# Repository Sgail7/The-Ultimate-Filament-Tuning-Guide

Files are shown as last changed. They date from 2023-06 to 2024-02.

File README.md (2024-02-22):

# The Ultimate Filament Tuning Guide

### How to tune 3D printer filaments to perfection!

This guide details how I tune in my 3d printing filaments. It takes approximately 80 grams of filament and a few hours of time, including print times. If your printer profiles are tuned in properly, following this guide will give you the best settings possible for your various filaments. This is **NOT** a guide on how to fine tune your printer's motion system and settings, for that, please see [Ellis' Excellent Print Tuning Guide](https://ellis3dp.com/Print-Tuning-Guide/). Both Ellis' and myself's Flowrate Test work, although I believe that my method gives more accurate results. Whichever you would like to use is up to you.

### Things to Know

This guide assumes that you are using [Klipper firmware](https://www.klipper3d.org/), but everything except for the probe calibration method is transferrable to any other 3D printer firmware. It also assumes that your are using [PrusaSlicer](https://www.prusa3d.com/page/prusaslicer_424/), however most, if not all, of these settings can be found in other slicers, although they may have slightly different names. Lastly, it assumes that you know how to slice for your machine and have a general knowledge of what the settings in your slicer modify. There is a plethora of knowledge online if you are confused. I highly recommend just looking up whatever you would like to know that isn't explained here.

All needed models and .3mf files are included in the [Tuning Models](Tuning-Models) folder. The guide will detail which file to use for each test. I highly recommend following the [Per Filament Steps](#per-filament-steps) section of the guide in order, as it will give the least variation in results, but you may follow this guide in whatever order you choose.

If you notice slight problems that can be attributed to a wrong interpretation of a test's results, I recommend finishing the entirety of the [Per Filament Steps](#per-filament-steps) section, and then going back and fixing the issue. Doing this prevents any untuned variables from skewing your retests, and means that once you fix the problem, everything is done and you can move on to printing!

# How to import 3MF files

Import the file into PrusaSlicer by **dragging and dropping it into the program**. If you use the `"Import Project..."` or `"Add..."` buttons, it will import the file with my personal profiles, which is a major headache. When the window shown below appears, make sure to select `"Import 3D models only"`. This will prevent you from importing my personal profiles and, again, will save a lot of headache getting rid of those.

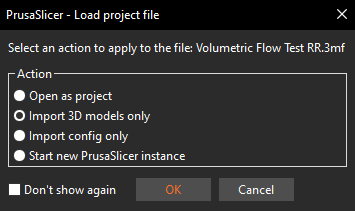
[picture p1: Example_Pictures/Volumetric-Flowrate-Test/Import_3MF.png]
3MF


# Feedback and Additions

This guide was created through my years of experience and the accumulated knowledge of this community. That being said information can be wrong, so if there is an issue with this guide, please open an issue on this repo! I'll get back to you and fix it as soon as I can. It doesn't matter if its a typo or an entirely wrong section, if something's not right, I'd like to make sure it's made right. 

If there is something that you think should be added to this guide, please submit a pull request or an issue! For example, I've been looking for good ways to tune the `Dynamic Fan Speeds` and `Enable Fan if Layer Print Time is Below:` settings!

Lastly, if you use this guide and find it helpful, please give it a star! It helps me know that other's find this guide useful and would benefit from it being updated whenever I figure out something new.

# THE GUIDE

- [One-Time Steps](#one-time-steps)
    - [First Layer Calibration](#first-layer-calibration)
    - [Elephant's Foot Compensation](#elephants-foot-compensation)
    - [Infill/Perimeter Encroachment Test](#infillperimeter-encroachment-test)
    - [Bridge Flow Rate Calibration Test](#bridge-flow-rate-calibration-test)

- [Per Filament Steps](#per-filament-steps)
    - [Temperature Test](#temperature-test)
    - [Volumetric Flowrate Test](#volumetric-flowrate-test)
    - [Linear Advance Test](#linear-advance-test)
    - [Flowrate Test](#flowrate-test)
    - [Retraction Test](#retraction-test)
    - [Fan Speed Test](#fan-speed-test)
    - [Minimum Layer Time Test](#minimum-layer-time-test)
    - [Minimum Layer Speed Test](#minimum-layer-speed-test)
    - [Validate Tuning Results](#validate-results)

- [Optional Steps](#optional-but-still-recommended-steps)
    - [Material Expansion/Contraction Calibration](#material-expansioncontraction-calibration)
    - [Retract/Unretract Speeds](#retraction-and-unretraction-speed-tuning)
    - [TMC Register Tuning](#tmc-register-tuning)
    - [VFA Testing and Tuning](#vfa-tuning-tests)

- [Troubleshooting Results](#troubleshooting-results)
    - [Validation Model Issues](#validation-model-issues)

# One-Time Steps

## **First Layer Calibration**

If using an automatic bed probe, first follow the klipper docs for [Probe Calibration](https://www.klipper3d.org/Probe_Calibrate.html).

- **Note:** The following is less of a one-time step and more of a "you should do this biweekly" step.

If your printer has bed leveling springs, run the `BED_SCREWS_ADJUST` command and use either a 0.10 mm feeler gauge or a sheet of A4 paper to adjust the bed to be in parallel with the gantry. Do this even if you have an automatic leveling probe installed.

When the above have been completed, make a cube in your slicer. Scale it to approximately half of the total size of your bed, then unlock the scaling and change the z height to be equal to the height of your first layer. Run the print while sitting infront of your printer. As the print progresses, use the babystepping feature found in your web interface to iteratively raise or lower the bed until your layer lines look perfect. Once you reach a point you are happy with, you can either let the print complete or cancel the print. Pull the layer of filament off of the bed and inspect the underside to make sure that your final adjustment is correct. Run `Z_OFFSET_APPLY_PROBE` then `SAVE_CONFIG` to save your new z-offset.

## **Elephant's Foot Compensation**
This isn't so much of a step as it is something that I just recommend doing. Elephant's foot compansation shrinks the first layer by the amount specified in the x and y axes so that your first layer squish doesn't artifically create a bigger-than-wanted footprint on the bed. I set this value at 0.1 mm to start. Typically it sits somewhere between 0 mm and 0.2 mm. I wouldn't recommend going above 0.2 mm unless you have a leveling problem, in which case you should redo the above step. If you make the elephant's foot compansation value too big, you may cause the first layer to be too small, preventing good layer stacking on top of it. You can read more about this feature [here](https://help.prusa3d.com/article/elephant-foot-compensation_114487).

## **Infill/Perimeter Encroachment Test**
- Uses [Perimeter-Overlap-Test](Tuning-Models/Perimeter-Overlap-Test.3mf)

Import [Perimeter-Overlap-Test](Tuning-Models/Perimeter-Overlap-Test.3mf) into your slicer. Make sure that there is at least two layers of infill between the top and bottom solid layers. Print out the file and check for gaps and pin holes at the edge of the top layer. The best value for your Infill/Perimeter overlap is where these gaps and holes disappear, but there is not over extrusion in the corners of the cube. The screenshot below shows what Perimeter Overlap Percentages each test model is printed at.

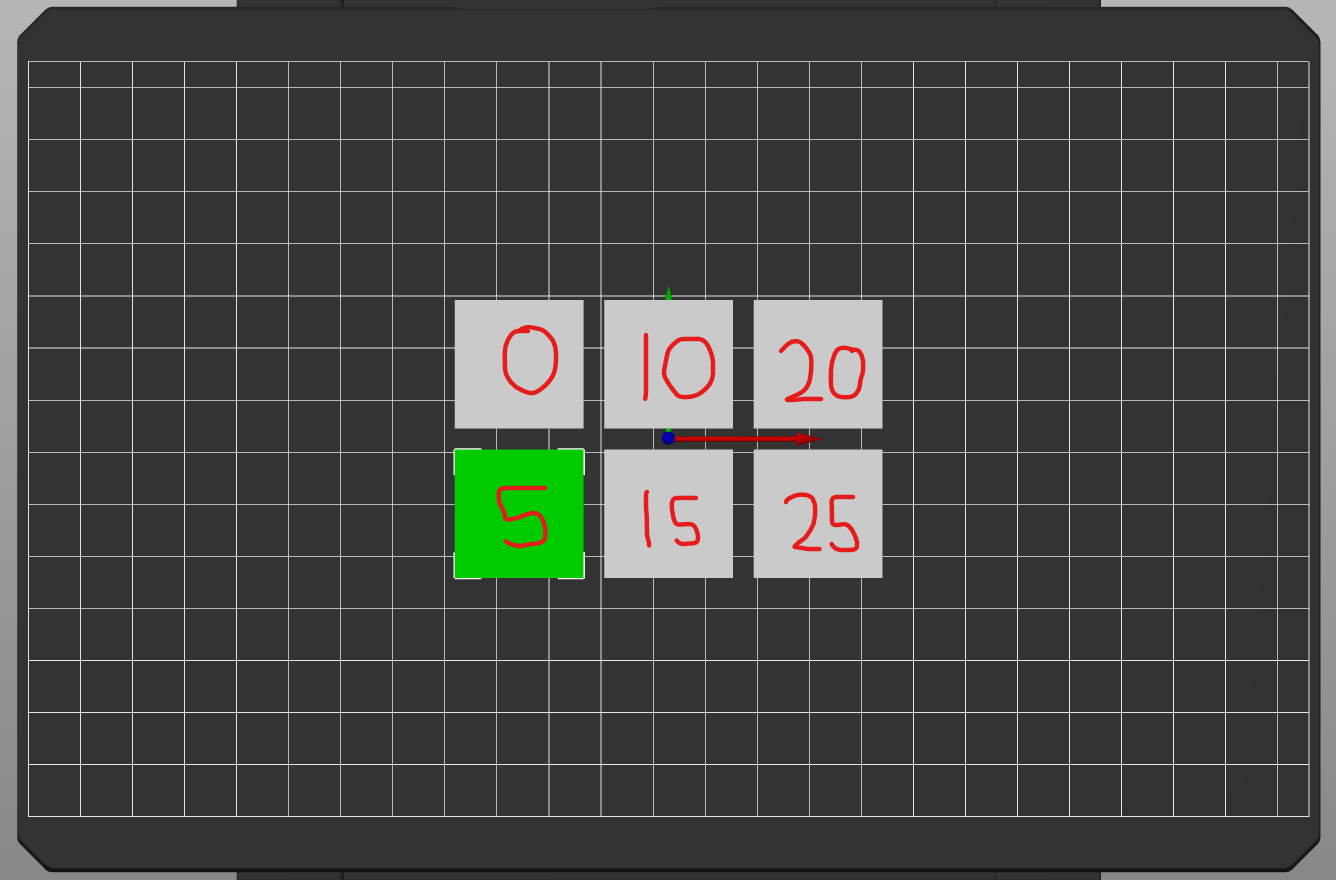
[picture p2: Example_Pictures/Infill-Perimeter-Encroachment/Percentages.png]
Perimeter-Overlap-Percentages


<details><summary>Click here to See Example</summary>
<p>

Overlap-Example

Here is an example of perimeter encroachment that I printed on my heavily modified Ender 3. The values used are the same as the screenshot from the slicer.

- A symptom of too little perimeter encroachment can be found in the 0% and 5% squares.
    - The pin holes at the edges of the top layer indicate that not enough filament is being extruded to properly bond to the walls.

- The 10% through 25% squares all show signs of too much perimeter encroachment.
    - The point where the top layer meets the walls causes a buldge at that contact point, rasing the edge of the top surface.
    - The beginning corner of the higher percentage squares can be seen to be severely over extruded. The 10% square has this also, but that is because the print ended in that spot.
    - It may be hard to see on camera, but the 20% and 25% squares also have ridges on their top surfaces that correspond to the extrusion lines on that surface, which is a result of over extrusion

From this test I can deduce that my ideal perimeter encroachment lies somewhere between 5% and 10%. To find this ideal encroachment, you can either change the values of the squares and run the test again (i.e. 5%, 6%, 7%, etc...), or you can change it as you do prints and finalize it when the top surface of those prints looks ideal.

Personally, I would recommend changing it by small amounts as you do prints. It won't affect your prints much, and will save you time and filament on another test print.

</p>
</details>

**Note**: Bigger nozzles usually have more difficulty closing these gaps. I recommend checking [this section of Ellis' print tuning guide](https://ellis3dp.com/Print-Tuning-Guide/articles/infill_perimeter_overlap.html) for more solutions.

## **Bridge Flow Rate Calibration Test**
- Uses [Bridge-Flow-Tuning](Tuning-Models/Bridge-Flow-Tuning.3mf)

This calibration should only be done after you have calibrated your fan speed and have figured out what a good bridging speed for your printer is. Make sure that your bridging still suffers even on 100% fan speed before using this feature. If you are satisfied with the bridging performance and dimensional accuracy of holes, skip this step, otherwise do the following.

Import [Bridge-Flow-Tuning](Tuning-Models/Bridge-Flow-Tuning.3mf) into your slicer. This file will print a group of the test model with bridge flow rates ranging from a bridge flow ratio of 1.0 to 0.4. The screenshot below shows the ratios that each test model is printed at.

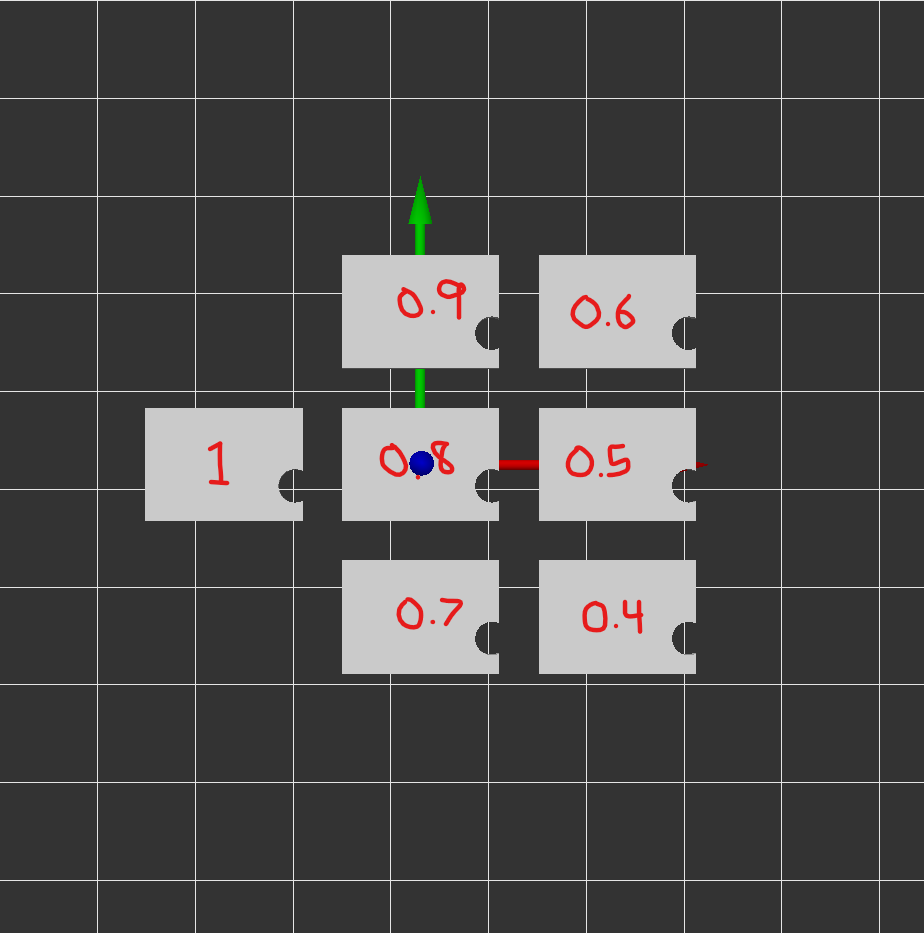
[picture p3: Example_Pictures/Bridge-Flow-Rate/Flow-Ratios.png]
Bridge-Flow-Ratios


Once these are printed, you are looking for the highest flow ratio that does not produce drooping at the top of the holes. You want to adjust this ratio as little as possible, the closer you can stay to a ratio of 1.0, the better. Once you have found your ideal bridge flow ratio, you can input the setting in the location shown in the screenshot below.

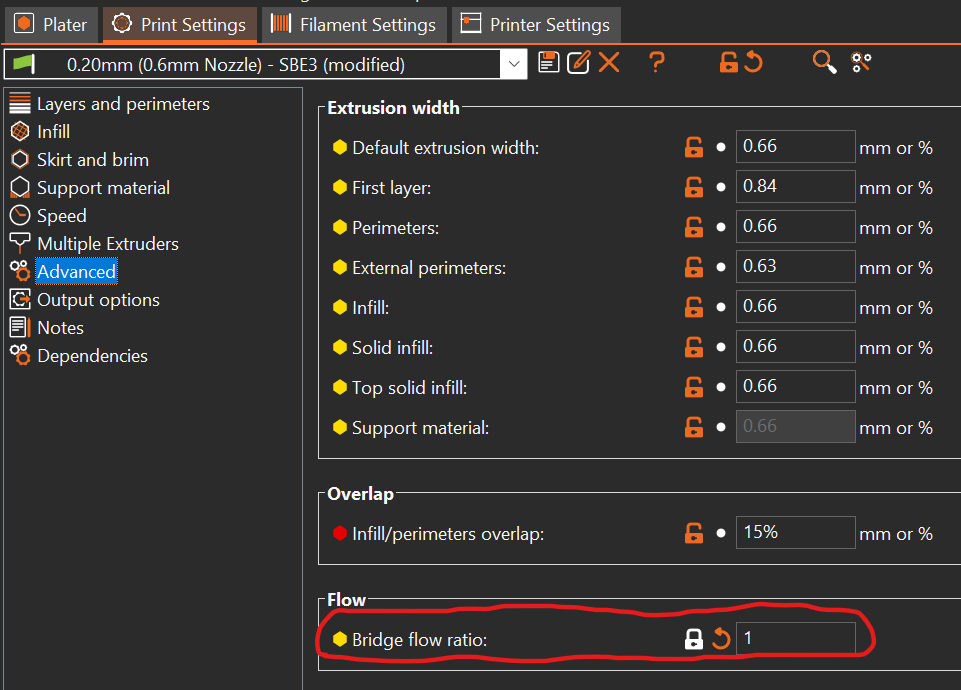
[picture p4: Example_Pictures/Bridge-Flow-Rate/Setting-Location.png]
Location-Bratio


Your final result should look something like this:

<details><summary>Click here to See Pictures</summary>
<p>

Here are a few pieces of the bridge flowrate test that I printed on my heavily modified Ender 3.

- This example was printed with a 1.0 ratio.
    - The top of the hole shows plastic that is severely protruding into the hole. This indicates that the flowrate is too high and needs to be lowered.

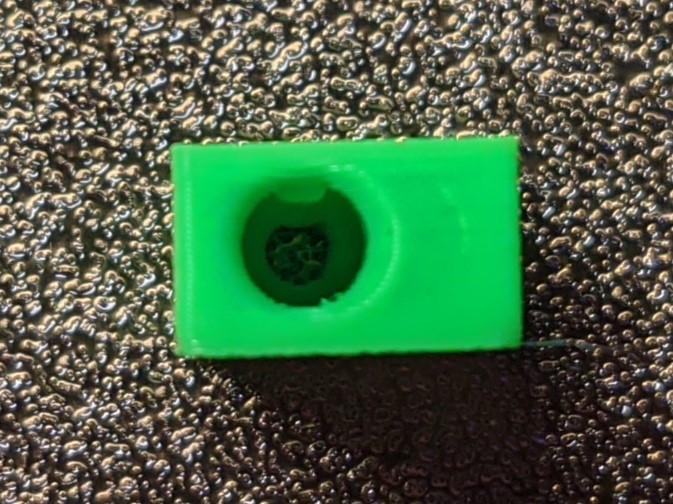
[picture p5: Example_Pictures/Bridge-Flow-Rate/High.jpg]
High


- This example was printed with a 0.4 ratio.
    - At the top of the hole, the bridging lines seem to be barely touching each other and in some cases being stretched thin near their ends. This indicates that the flowrate is too low and needs to be raised.

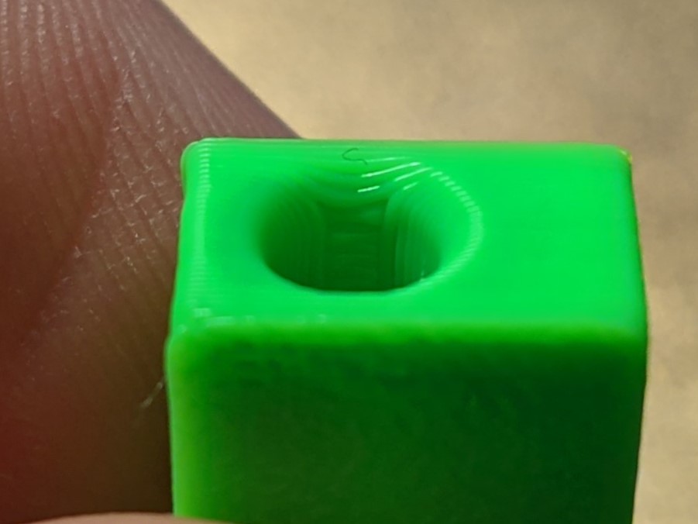
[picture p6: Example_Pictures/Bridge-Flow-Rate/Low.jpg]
Low


- This example was printed with a 0.7 ratio.
    - The bridge lines at the top of the hole are nice and even, touching their neighbors without protruding into the hole. This is the correct flowrate for this printer and infact is the flowrate I use for a 0.20 mm layer height, which is what is pictured.

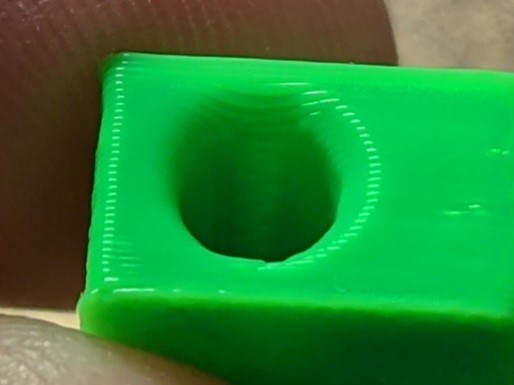
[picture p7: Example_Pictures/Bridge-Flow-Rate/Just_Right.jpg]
Correct


- **Note:** It is very hard to take pictures of this feature because of the size of the pieces and lighting. I promise that the differences between the flowrate ratios are much more clear when doing this test in real life.

</p>
</details>

**Note**: You will have to test this for every layer height profile that you have for your printer. Since different volumetric amounts are output at different layer heights, the amount of bridge flow rate reduction needed will vary. Generally, more is needed for larger layer heights, and less is needed for smaller layer heights. You are trying to get away with as little flow reduction as possible. Going too low on the multiplier may cause poor support for the layers on top of it or, in extreme cases, a breaking of the filament flow, causing the bridge to fail entriely (you will have to make a conceited effort to achieve the latter).

# Per Filament Steps

## **Temperature Test**

**Note:** For this test, you will need to unlatch your extruder in some way. Whether that be removing the tension knob on a bondtech gear set or holding the lever arm open on a Mk8 style extruder. Essentially you don't want the extruder gear(s) touching the filament in anyway, if possible.

Read the manufacture's rated temperatures for your filament. Choose a starting point that is 10°C below the lowest temperature, and an ending point that is 10°C higher than the highest temperature. For example, a range of `190°C - 220°C` would mean that you want to run the hotend through a temperature range of `180°C - 230°C`. Set your hotend to your starting point and let it stabilize.

Unlatch your extruder and grip the filament with your hand. The goal is to push filament through the extruder with as constant of a pressure as possible. Once in position, set the temperature of your hotend to your ending point, and start pushing. Keep a close eye on the temperature as it rises and as you keep pushing.

You will notice that the filament starts moving noticably faster when the hotend hits certain temperatures. Make a note of those points in your head as you push the filament. Once the hotend reaches your chosen ending point, you can stop pushing the filament. Turn your hotend heater off and relatch your extruder.

Write down the tempatures where you noticed the resistance on the filament decrease. Generally, picking a temperature in the middle of the manufacture's rated temperatures is a good all around setting. Avoid the trap of setting the filament temperature as low as possible, as it can lead to extruder skipping and extruded lines that were not fully melted in the hotend.

Continuing the example from earlier, say there's a filament with a rated temperature range of `190°C - 220°C`. I'll set my hotend to run through a range of `180°C - 230°C` for this test. I do the test as described above, and I find that the points at which the resistance on the filament dropped were `190°C, 210°C, and 230°C`. Wanting a good overall setting, I'll choose `210°C` as the temperature for this filament.

### Good Rules of Thumb

- Generally, the best temperature is somewhere in the middle of the recommended temperatures on a standard 0.4mm brass nozzle, however, this is not a steadfast rule. Hardened steel nozzles tend to need to run about 10-15 C hotter than brass to compensate for their lower heat transfer coefficient.

- Adding 5°C to your chosen temperature can be beneficial if you tend to prefer setting your filaments to lower temperatures. It will prevent your filament from being too resistive to extrusion while still maintaining the qualities that you are looking for.

- If pushing for high volumetric flow rates, chosing the highest temperature where the resistance on the filament dropped is the best option for this test. Keep in mind that doing this will cause lower volumetric flow rate areas in your models to string more heavily.

## **Volumetric Flowrate Test**

- Uses [Volumetric-Flow-Test-RR.3mf](Tuning-Models/Volumetric_Flow_Test.3mf)
- This test was designed by Yathani on Printables! Go check it out here: [Volumetric Flow Test for RatRig V-CORE3](https://www.printables.com/model/328223-volumetric-flow-test-for-ratrig-v-core3)

This test works by increasing your printer's feedrate by 100% every 5 mm in z-height. For a standard flow hotend, you'll want to step up in 2 mm<sup>3</sup>/s increments; for high-flow hotends, you'll want to step up 2-5 mm<sup>3</sup>/s increments, depending on the advertised maximum flowrate of your hotend. The final volumetric flowrate will be 12 times the starting flowrate.

Volumetric flow rate can be calculated as:

$$VFR=Layer height * Layer width * Layer Speed$$

Because layer height and layer width stay constant during a print, we want to change the layer speed of the external perimeters to control the volumtric flowrate of the test. Rearranging the equation, and using 2 mm<sup>3</sup>/s as the target volumtric flow rate, we can find our needed external perimeter speed for this print.

$$Layer Speed=2/(Layer width*Layer height)$$

Using a 0.4mm layer width with a 0.2mm layer height as an example, we obtain this answer

$$Layer Speed=2/(0.4*0.2)$$

$$Layer Speed=25mm/s$$

Turn on Spiral Vase mode, set your external perimeter speed to the value you obtain, and run the print. If you feel that the final volumetric flow rate is far past the limit of your hotend, you can scale the model in z-height only in PrusaSlicer to obtain a lower final volumetric flow rate.

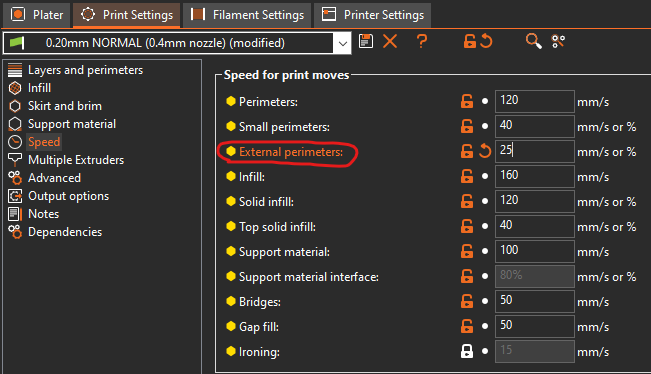
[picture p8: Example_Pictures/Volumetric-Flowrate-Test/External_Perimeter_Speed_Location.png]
External-Perimeter-Location


Once this test is completed and your printer is cooled, I highely recommend either restarting the printer, or, if using Klipper, issuing a `FIRMWARE_RESTART` command.

## **Linear Advance Test**
- Follow [Ellis' Print Tuning Guide](https://ellis3dp.com/Print-Tuning-Guide/) for this and use [his online calibration tool to generate your gcode.](https://ellis3dp.com/Pressure_Linear_Advance_Tool/) Do interations down to 0.001 for Direct Drive extruders, and down to 0.01 for Bowden extruders.
- [Ellis' Pressure Advance Documentation](https://ellis3dp.com/Print-Tuning-Guide/articles/pressure_linear_advance/pattern_method.html)
- [Klipper Pressure Advance Documentation for Extra Information](https://www.klipper3d.org/Pressure_Advance.html)

- **Note:** If flowrate is wildly off target, running pressure advance and using the value found can exacerbate the issue. In these instances, running the Linear Advance Test again after the Flowrate Test can alleviate these issues. Typically, anything greater than a 10% deviation of flowrate requires a recalibration of Linear Advance with the newly found flowrate.

As I've explained in the [Retraction/Unretraction Speed Tuning Section](#retraction-and-unretraction-speed-tuning), I am not a fan of external gcode generators. However I feel the need to explain my preference for this method of pressure advance calibration, as I used to recommend the [Official Klipper](https://www.klipper3d.org/Pressure_Advance.html#tuning-pressure-advance) method.

I have found that using the Klipper Tuning Tower Method has reliably and repeatedly given me pressure advance values that are higher than what a filament requires. These values lead to print artifacts that round off corner entries, create wall separation, and cause very high [Infill/Perimeter Overlap](#infillperimeter-encroachment-test) values to be needed. Because each of these issues can also be caused by other variables, and they are seemingly unrelated when not considering specifically pressure advance, it can lead one on a wild goose chase trying to solve the issue.

In addition to that, it can be very hard to tell what a good pressure advance value is due to each of the corners of the model showing different amounts of artifacting. Trying to measure the inside small corners of the model is more accurate, but is a pain with calipers and impossible with a micrometer of reasonable size.

In contrast, Ellis' pattern method is more accurate, faster, and uses less filament. It's only two downsides are that it requires iterations and an external gcode generator. Despite that I exclusively use this method now to avoid the afformentioned issues and gain from the afformentioned benefits.

## **Flowrate Test**

Create a 25mmx25mmx25mm cube in your slicer. Set your slicer to Spiral Vase mode, and take note of your external perimeter line width. You should be printing an object similar to the following.
    
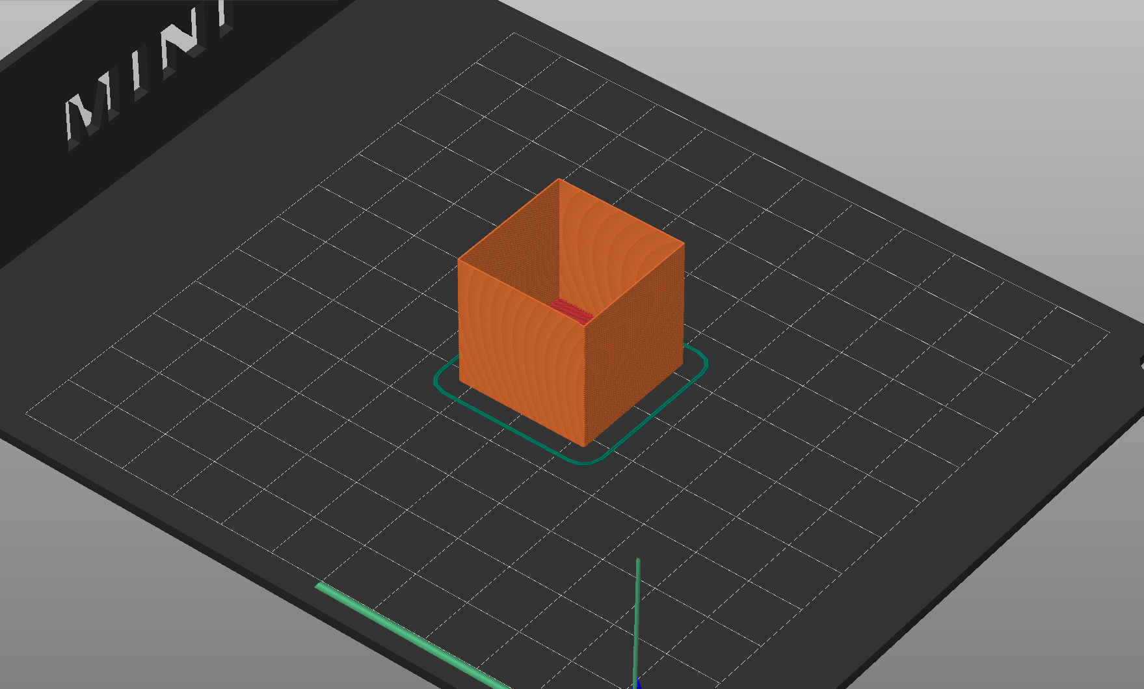
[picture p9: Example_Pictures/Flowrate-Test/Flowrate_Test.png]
Flowtest-Example


Allow the cube to cool before removing it from the buildplate, then take a pair of calipers and measure the thickness of each wall. I only recommend putting the calipers, at maximum, ~2mm down the sides of the cube to prevent excessive variation from layer wobble. Take the average of your measurements, then divide your line width by that average. This will give the correct flowrate for the tested filament.

Example: Line width is set to 0.45mm. The cube's walls are found to have a line widths of 0.45, 0.47, 0.48, and 0.46, respectively. The average of those line widths is equal to:

$$Average=(0.45+0.47+0.48+0.46)/4$$

$$Average=0.465mm$$

To find the needed flowrate multiplier, divide the original line width by the found average:

$$Flowrate=0.45/0.465$$

$$Flowrate=~0.968$$

This would be the new flowrate multiplier for your filament. If you notice underextrusion issues in your prints, try increasing your multiplier by 0.01.

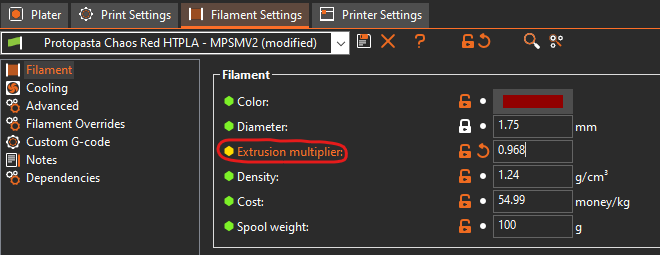
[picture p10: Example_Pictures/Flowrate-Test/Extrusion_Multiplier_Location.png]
Flowrate-Location


- +-2% flow rate is negligible due to variation of filament diameter. In other words, if your result returns a number between 0.98 and 1.02, don't change your flow rate, it will cause more problems than it will solve.

## **Retraction Test**

- If you haven't noticed any problems with stringing, and don't notice any in the Fan Speed Test, this step can be skipped. Generally, with a good direct drive setup, the only filaments that will need a different retraction value are very soft flexible filaments and exotic filaments such as Carbon Fiber filled PLA.

Take the config that you have been using so far, and export it from PrusaSlicer. 
    
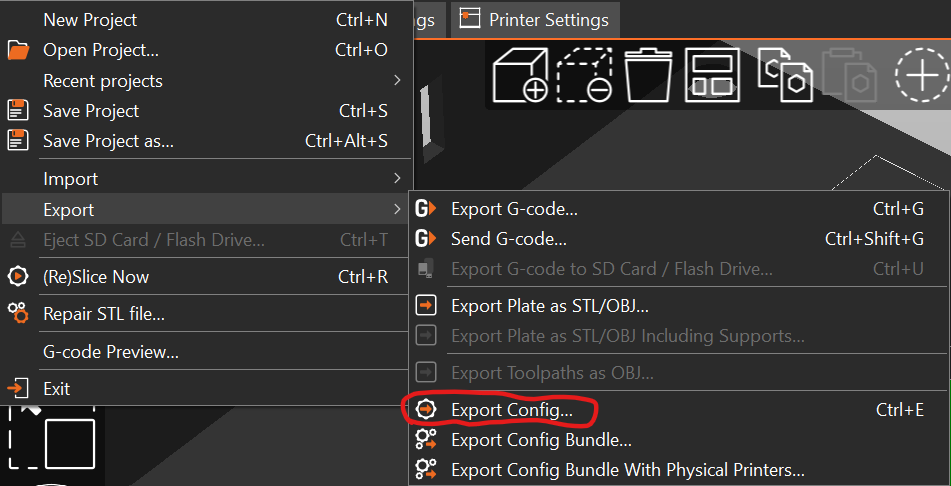
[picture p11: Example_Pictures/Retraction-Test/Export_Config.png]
Config-Export

    
Import it into SuperSlicer and save it. Now, use the built in Retraction Calibration that SuperSlicer has to determine the retraction needed for your particular filament. Read through the prompt that appears when you set up the test, it will tell you everything that you need to know to preform it.

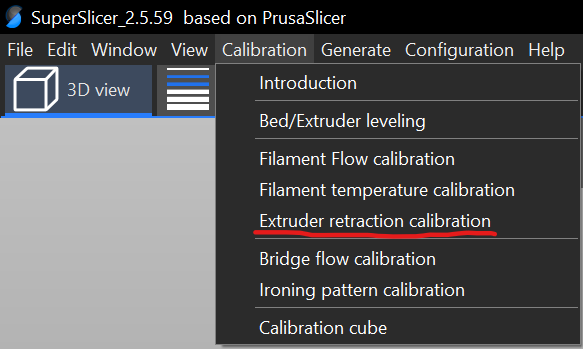
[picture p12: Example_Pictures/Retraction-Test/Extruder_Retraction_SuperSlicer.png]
SuperSlicer-Retraction-Test


## **Fan Speed Test**

- This test was designed by Abyss on Printables! Go check it out here: [Ultimate Fan Speed Test V3](https://www.printables.com/model/200347-ultimate-fan-speed-test-v3)

**Note:** Fan speed is generally forgiving. If you are getting worse results than expected you can raise or lower any of the fan speeds you set in this step. This step always gets me perfect fan speeds, but it may take some practice before you gain a feel for how to choose settings with this method. Essentially, you're not locked in to what you choose, just use it as a guideline.

- Import [Ultimate_Fan_Test_v3_ABYSS.stl](Tuning-Models/Ultimate_Fan_Test_v3_ABYSS.stl) into your slicer. Use a 0.2mm layer height and change your cooling settings to the following.

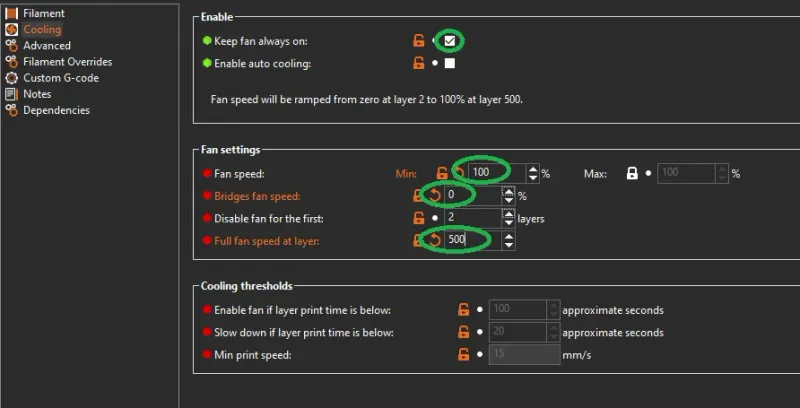
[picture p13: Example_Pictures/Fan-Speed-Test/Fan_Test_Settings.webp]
Fan_Speed_Settings


This will cause your fan to spin progressively faster as the model is printed, starting at 0% fan speed and ending at 100% fan speed. When the model is finished, take a look at each marked bar and the area above it. Choose the lowest fan speed that gives good results as your minimum fan speed. Generally, no curling and decent to good looking bridges are what to look at for this setting. Look at the bridging sections and choose the one that looks the best to you, that is your bridging fan speed.

You may want to take a picture of your model, because the next step involved intentionally breaking it apart. Start from the top of the model and work your way down, breaking it apart section by section. The sections will get harder to break apart as the fan speed at the point in the model gets lower. As you break it apart, feel for where the model gets harder to snap. There should be a point where it doesn't get any harder, and that is where your maximum layer adhesion is achieved. Take note of the highest fan speed at which the model has the same resistance to breaking as your chosen minimum fan speed. Set this fan speed to your maximum fan speed.

## **Minimum Layer Time Test**

- Uses [Minimum-Layer-Time-Test.3mf](Tuning-Models/Minimum-Layer-Time-Test.3mf)

Set your minimum layer time to 5 seconds and print this model. If the outer walls of the print curl up, increase the minimum layer time by two seconds. Print the model again with the new minimum layer time setting and check if there is any curling. Repeat this process until the walls print flat. Whatever you minimum layer time is at that point is the ideal value for that setting.

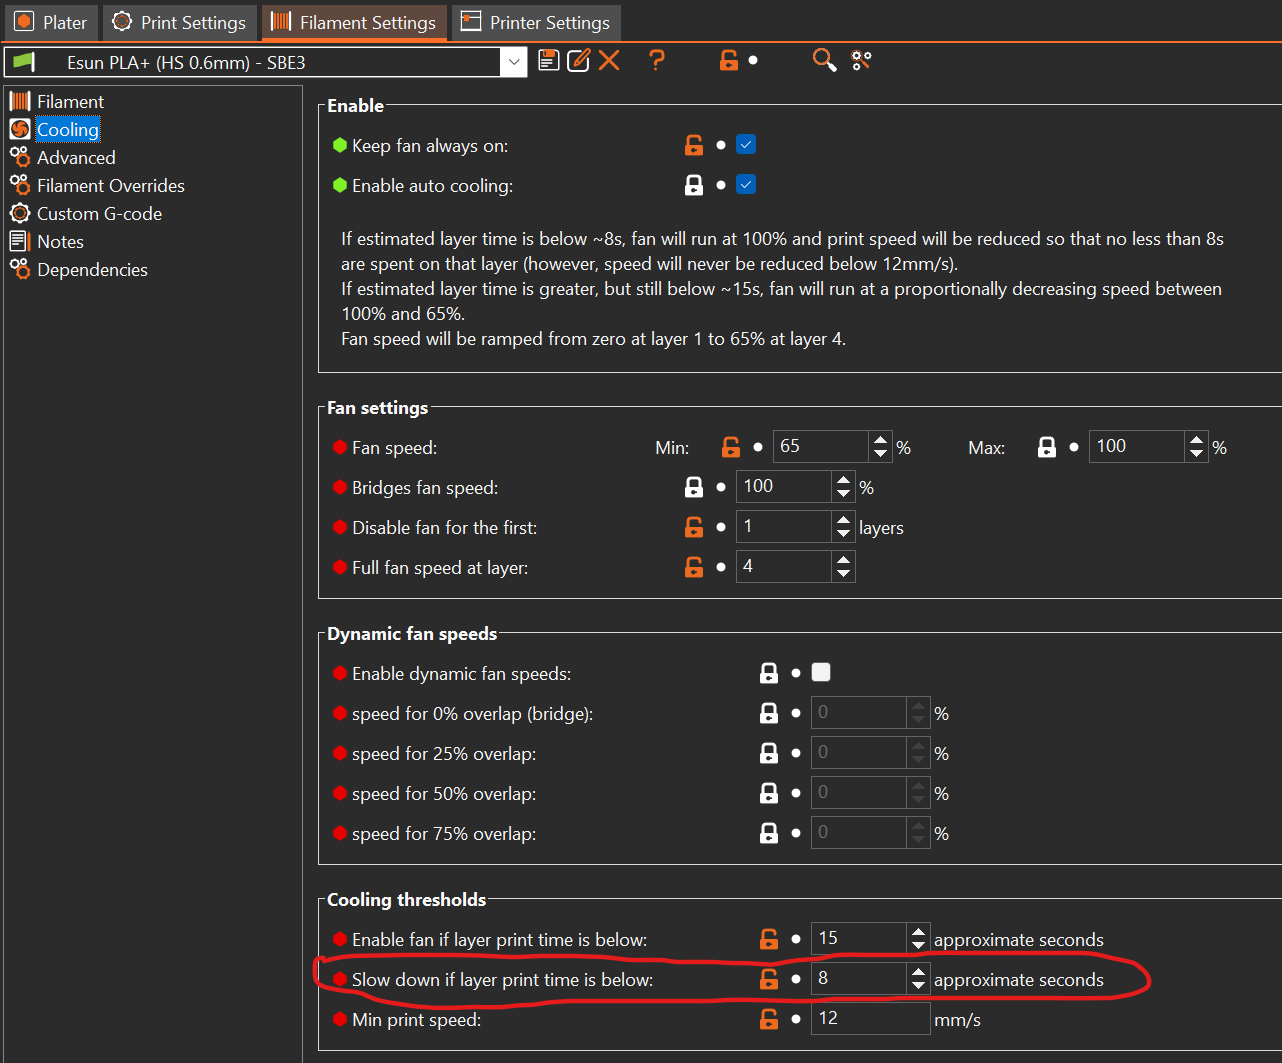
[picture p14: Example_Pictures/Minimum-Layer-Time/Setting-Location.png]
Location-Ltime


**Note:** For some filaments, there may not be a minimum layer time value that will completely eliminate curling. If this is the case, you can try lowering your printing temperature by a few degrees or upgrading your cooling setup. Otherwise, just choose the setting that gives the best results, even if they aren't perfect.

## **Minimum Layer Speed Test**
- Uses [Minimum-Layer-Speed-Cone.stl](Tuning-Models/Minimum-Layer-Speed-Cone.stl)

I recommend printing 5 copies of this model set at the following minimum layer speeds, `15 mm/s, 12 mm/s, 10 mm/s, 8 mm/s, 5 mm/s, and 3 mm/s`. Label each of the models as you print with a sharpie or other method, so that you do not forget which one is which. Put the printed models side by side and compare them to see which has the least amount of deformed plastic at the top of the model. Set this speed as your minimum layer speed.

**Note:** The upper 5 mm or so of this model will never look perfect as it is unresonable to expect that kind of accuracy from a 0.4mm nozzle. Once you find a speed that you are happy with, save it, set it, and forget it. Going too low in speed will cause problems seen at higher speeds to creep back in. This happens because the nozzle has more time in contact with a specific layer at slower speeds, eventually causing it to heat the filament more than the extra cooling can compensate for. 

The sweet spot can be found where the nozzle is moving slow enough to allow the part cooling to work effectively, but fast enough that the nozzle is not reheating the filament after it has been deposited.

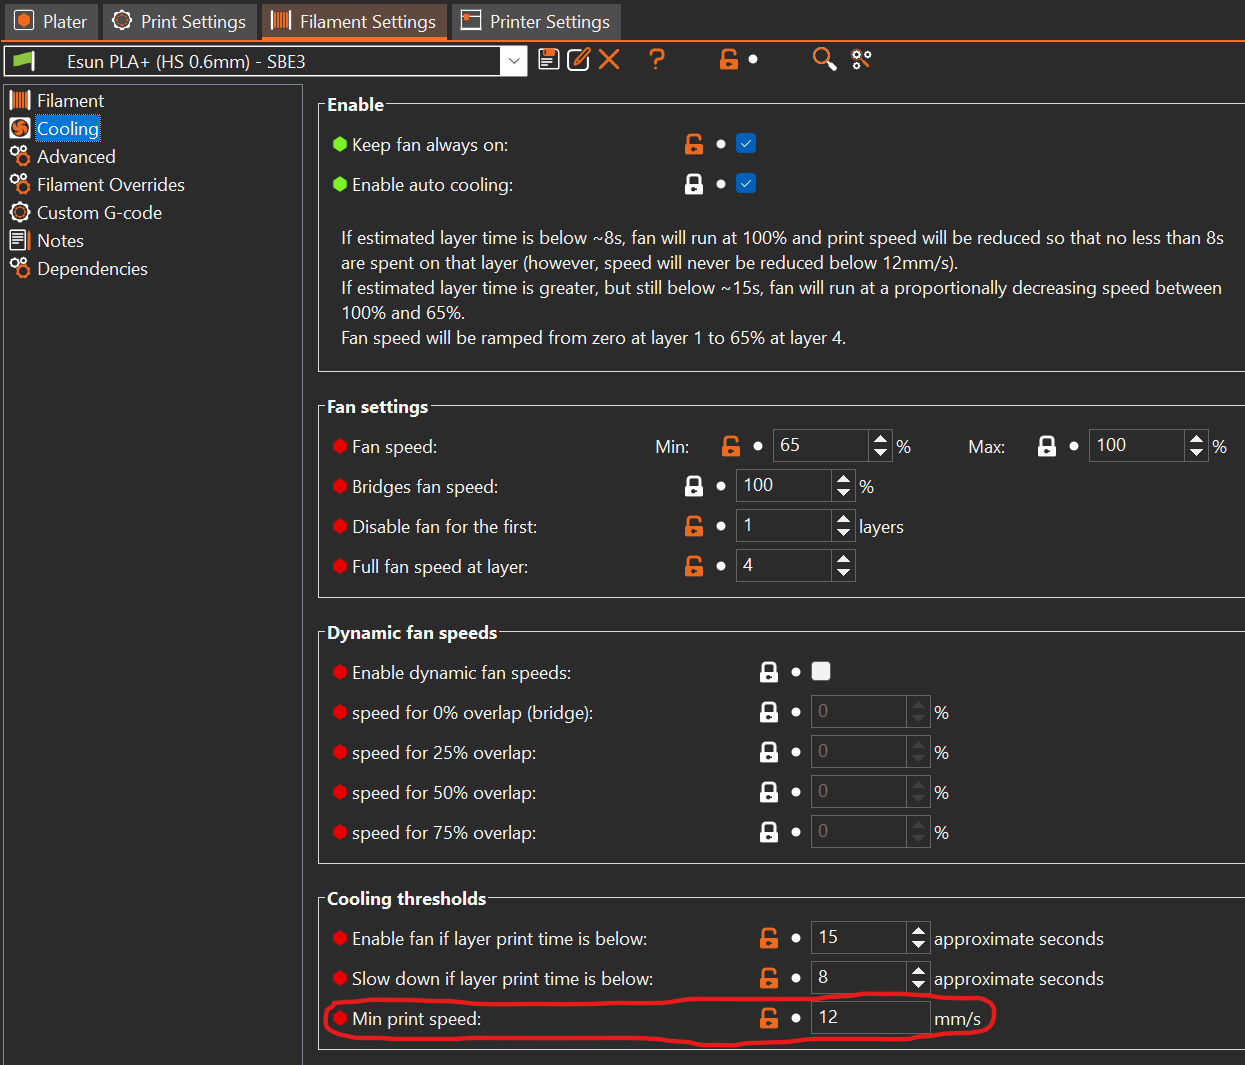
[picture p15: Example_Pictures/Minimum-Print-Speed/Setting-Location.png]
Location-Lspeed


## **Validate Results**
- Print a [Voron Cube](Tuning-Models/Voron_Design_Cube_v7.stl) to validate bridging and corner accuracy.
- Print a [Cali Dragon](Tuning-Models/Cali-Dragon_v1.stl) to validate small detail quality, layer quality, and cooling characteristics.

# Optional (but still recommended) Steps

## Material Expansion/Contraction Calibration

- Finding this setting is useful for using filaments such as ABS. It is worth noting however, that well designed parts such as things designed by the Voron Team have been designed with shrinkage already in mind. This means that if you were to use your expansion settings on those parts, they would be printed incorrectly.

- If the x, y, and z give different percentages of shrinkage, you will want to scale your parts by those three values in each of their respective axes. Filaments don't always scale exactly the same in all axes.
- Some brands like ProtoPasta provide datasheets for their High Temp filaments that give scaling factors for annealing. I recommend following those first for those filaments and testing your results, then following this section with those compensations already put in place **ONLY** if you have problems. Chasing perfection with this kind of process will only lead to disappointment.

Start by slicing a 25x25x25mm cube in your slicer on your normal settings. Print this cube in PLA or another control filament that doesn't shrink or expand much.

Measure the length, width, and height of the cube with calipers. Now, slice another 25x25x25mm cube and print it in the filament you are testing. Measure the length, width, and height of this cube, and compare it to the control cube.

Divide the control cube's length, width, and height by the test cube's length, width, and height. Take those three values and average them. This is the value by which you will want to scale all models printed in that filament to maintain the intended dimensional accuracy. An example of this can be seen below.

$$ControlCube=25.1mm*25.2mm*25mm$$

$$TestCube=24.8mm*24.8mm*24.8mm$$

Now, find the average of the x, y, and z directions:

$$average_x=(25.1/24.8)=1.012$$

$$average_y=(25.2/24.8)=1.016$$

$$average_z=(25/24.8)=1.008$$

$$average=(1.012+1.016+1.008)/3$$

$$average=1.012$$

In this example, this is the expansion multiplier you would use for the test filament. If your slicer scales in percentages, that answer translates into 101.2%.

## Retraction and Unretraction Speed Tuning

- **Note for geared extruders:** There is a point, typically from 40-50 mm/s, where your extruder will start skipping steps on retraction. If you find that you are needing speeds this high, consider drying your filament or retuning retraction. If you still go ahead with those speeds, sit and watch your printer while the test prints and listen for the extruder motor skipping steps.

- Typically the retraction/unretraction speed that your printer ships with is good for printing with. This is one of those settings that makes a relatively small difference once you get past settings that are too slow.

- After completing this tuning, it is a good idea to go back and retune your retraction distance. I have had my retraction distance change by as much as 2mm after doing this tuning on bowden printers.

Once you have completed the [Retraction Test](#retraction-test) portion of this guide, you may also tune your Retraction and Unretraction speeds. This will be achieved through the use of [Teaching Tech's 3D printer calibration website](https://teachingtechyt.github.io/calibration.html#retraction).

Navigate to the "Retraction Tuning" tab, if the hyperlink above does not take you there. Once there, scroll down until you see the "Retraction" section. Once there change your Retraction distancee to what you are currently using for all heights. Then increment your Retraction and Prime (unretract) speeds in increments of 5 as seen in the picture below.

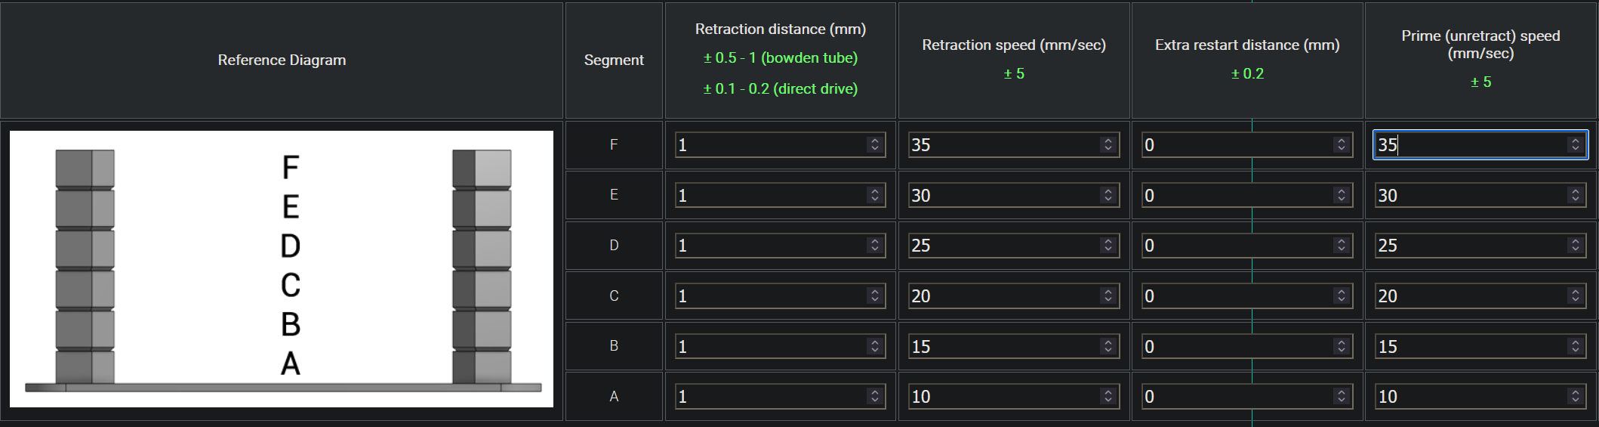
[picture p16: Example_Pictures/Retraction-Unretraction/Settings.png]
retract-unretract-settings


Change the rest of the settings in the tool to match what you use on your printer, and then export the gcode. **MAKE SURE TO CHECK THIS GCODE BEFORE RUNNING IT**. Using your slicer's gcode viewer is a good way to do this. I generally don't like using external gcode creation websites, because it is easy to put in a wrong setting and cause your printer to do something unwanted.

Run the print and mark what speed gives you the best results. If desired, the retraction and unretraction speed can be tuned separately to give you more accurate results.

## TMC Register Tuning

Still in the process of researching this.

## VFA Tuning Tests

Still in the process of researching this.

# Troubleshooting Results

## Validation Model Issues

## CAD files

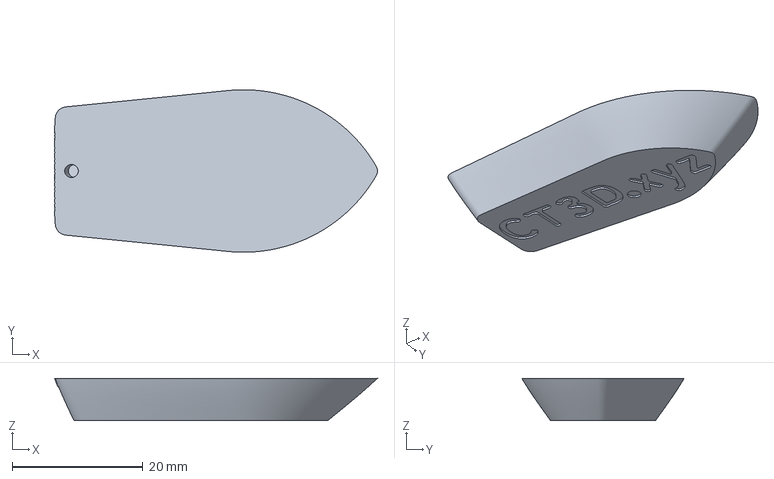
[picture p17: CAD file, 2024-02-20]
Tuning-Models/Minimum-Layer-Time-Test.3mf
49.5 x 24.9 x 6.50 mm

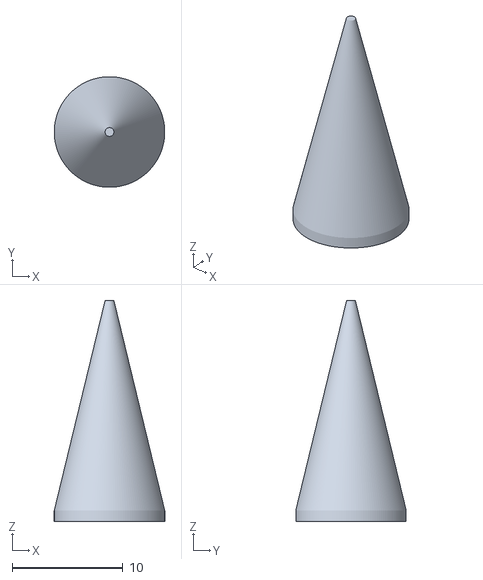
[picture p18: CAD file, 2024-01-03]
Tuning-Models/Minimum-Layer-Speed-Cone.stl
10.0 x 10.00 x 20.0

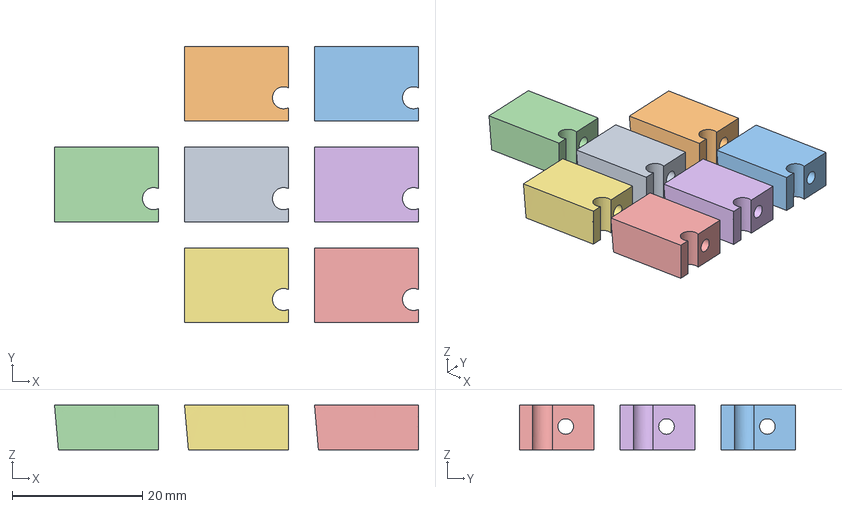
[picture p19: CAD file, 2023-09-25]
Tuning-Models/Bridge-Flow-Tuning.3mf
56.0 x 42.5 x 6.88 mm
Bridge-Flow-Tuning.stl x 7

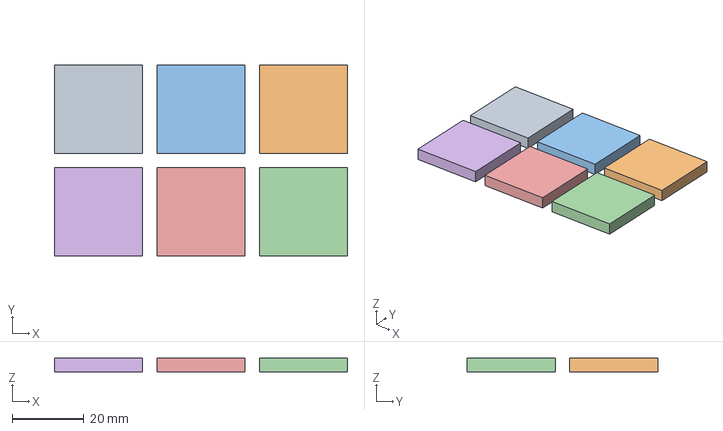
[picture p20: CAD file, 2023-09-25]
Tuning-Models/Perimeter-Overlap-Test.3mf
81.8 x 53.2 x 4.00 mm
Shape-Box x 6

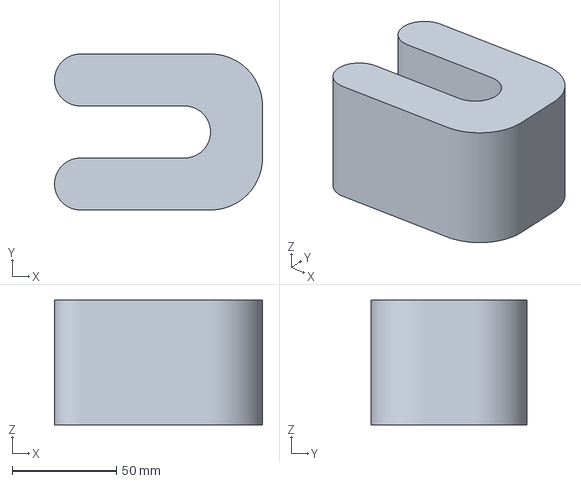
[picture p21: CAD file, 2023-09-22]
Tuning-Models/Volumetric_Flow_Test.3mf
100.0 x 75.0 x 60.0 mm

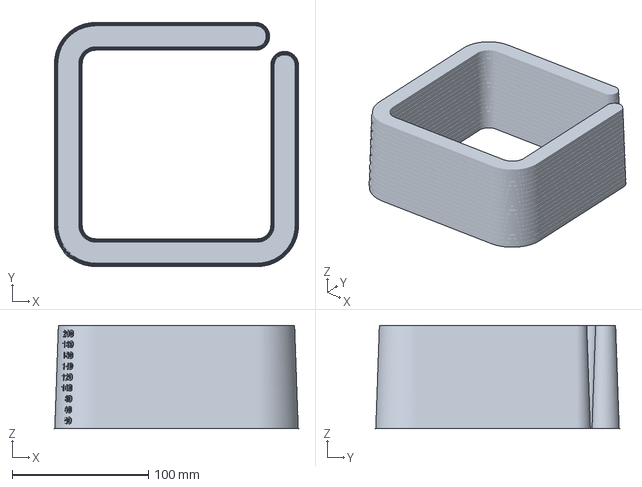
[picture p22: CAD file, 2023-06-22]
Tuning-Models/motor-test-PrusaSlicer-PLA.3mf
179.4 x 179.4 x 76.0 mm

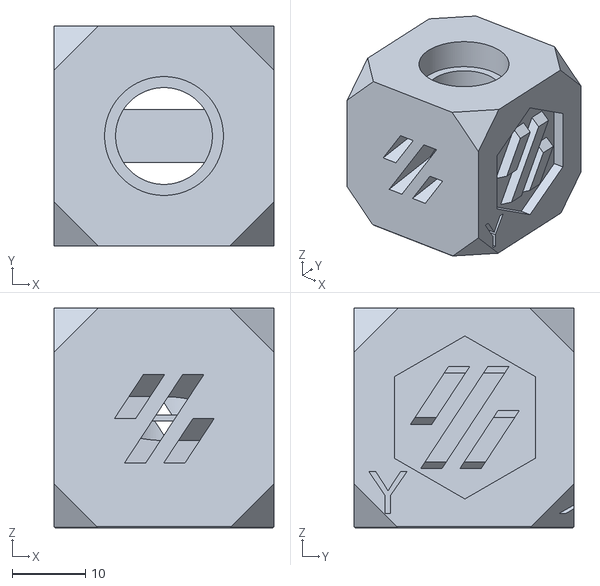
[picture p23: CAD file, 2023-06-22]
Tuning-Models/Voron_Design_Cube_v7.stl
30.0 x 30.0 x 30.0

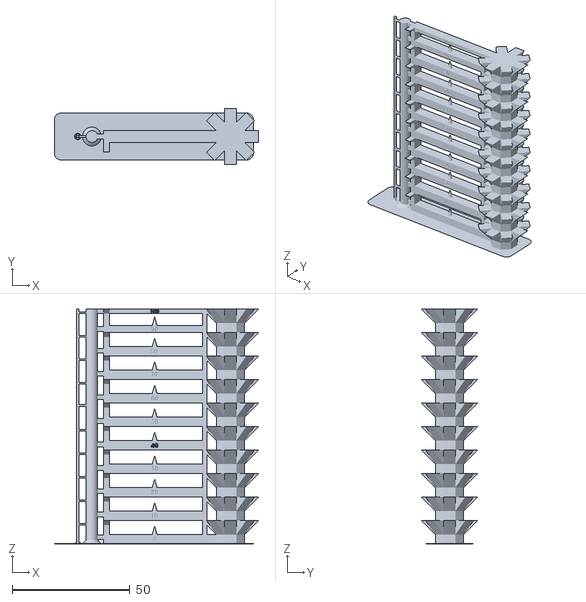
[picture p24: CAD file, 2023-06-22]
Tuning-Models/Ultimate_Fan_Test_v3_ABYSS.stl
87.0 x 24.0 x 100.0

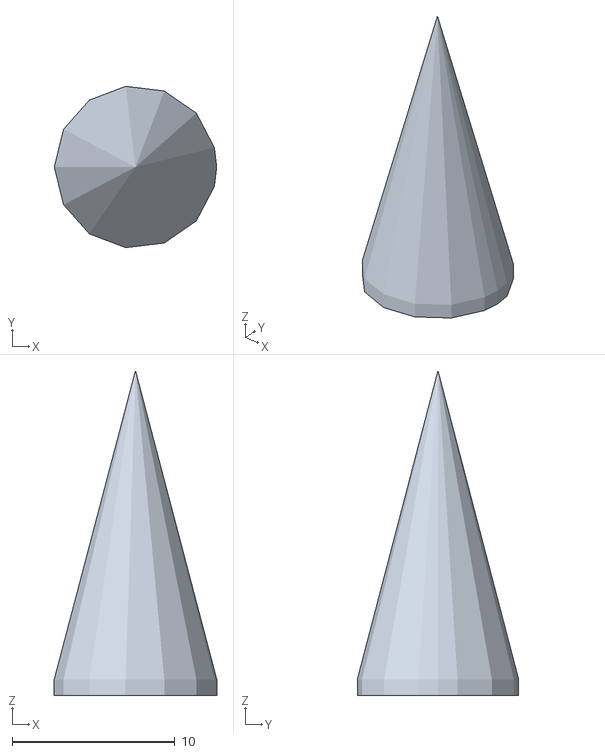
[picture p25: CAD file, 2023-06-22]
Tuning-Models/Test_Pieces_Cone-10mm-Tall.stl
10.0 x 9.93 x 20.0

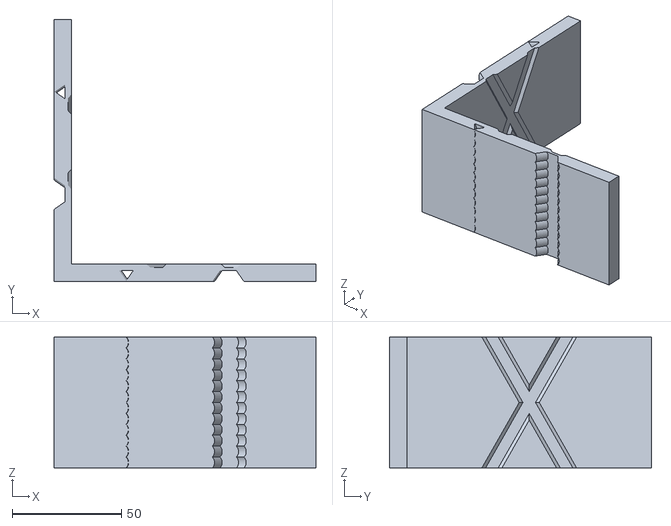
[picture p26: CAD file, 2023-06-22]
Tuning-Models/ringing_tower.stl
120.0 x 120.0 x 60.0

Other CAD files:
Tuning-Models/VFA-Cure-Test.3mf

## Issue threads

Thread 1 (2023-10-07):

A note for flow calibration before retraction

jake161, 2023-10-07:
In certain circumstances when flow is wildly incorrect before calibrating, pressure advance can exaggerate the issue. I would recommend getting an approximate flow value first before running PA.

Sgail7, 2023-10-11:
I will add this note in the upcoming commit. Thank you for the catch!

Sgail7, 2023-10-16:
Issue fixed in Commit #17

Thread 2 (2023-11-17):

Perimeter Encroachment Test 3MF

jake161, 2023-11-17:
When opening the 3MF for perimeter encroachment it tries to import Makerbot R2X profiles as well as a klipper estimator post processing script that throws a warning.

jake161, 2023-11-18:
Hey I retried the import after rereading the guide and I believe there may be an incompatibility with PrusaSlicer 2.7 Alpha. I don't get the dialogue for importing models only when both using the "open project" option or the "add" option. Any ideas?

jake161, 2023-11-20:
Update:

After some experimentation, it seems that the dialogue for importing models only appears only when you drag the file into PrusaSlicer. An odd feature choice to be sure, but that seems to resolve the issue.

Sgail7, 2023-11-23:
Interesting... I've been able to recreate this behavior with the last stable release of PrusaSlicer 2.6.1. It seems that once you set your preference according to the "How to Import 3MF Files" section, using the "Add..." button on the main screen will import only the model of the 3MF, omitting the original profiles. However, if you use the "Open Project..." option under the "File" drop down menu, it will import the model with the original profiles no matter what. A very inconvenient design decision, but not much that can be done about it.

I'll add clarification to the "How to Import 3MF Files" section to make sure no one else runs into this unexpectedly. I'll also make that section stand out a little more as I've had complaints of it being too hidden. Thanks for bringing this to my attention!

Sgail7, 2024-01-03:
Issue resolved in Commit #19.

Closed 2024-01-03.

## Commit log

2023-06-22 Add Initial Information
    Basically just copying over what was in my notes
    [Minimum Layer Time Test.3mf, Stringing_Test.stl, Test Pieces_Cone 10mm Tall.stl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]
2023-06-22 Added Information for the Mandatory Steps and Bridge Flow Tuning Model
    [Bridge Flow Tuning.stl, Minimum Layer Time Test.3mf, Stringing_Test.stl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]
2023-06-23 Added some pictures
    [Volumetric-Flow-Test-RR.3mf]
2023-06-23 Added some more links and extra picture
    [Bridge-Flow-Tuning.stl, Minimum-Layer-Time-Test.3mf, Test_Pieces_Cone-10mm-Tall.stl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]
2023-09-22 Update VMF model and Readme
    [Volumetric-Flow-Test-RR.3mf, Volumetric_Flow_Test.3mf]
2023-09-25 Add a bunch of pictures and clean up writing
    [Bridge-Flow-Tuning.3mf, Perimeter-Overlap-Test.3mf]
2023-11-14 Tuning Updates and Clarification
    Changed recommended method of linear advance tuning. Adding a section talking about why you might want to use the new method instead of the old.
    Added section to fan speed tuning to describe breaking model apart to verify layer adhesion.
    Expanded upon and clarified the Temperature Test, hopefully making it both easier to understand and to reproduce.
    Cleaned up tuning model folder, making it less confusing to navigate.
    Added some more hyperlinks throughout the readme to things both within itself and outside of it.
    Remove the last link to the manual bed leveling section RIP ;(
    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
    [Bridge-Flow-Tuning.stl, Stringing_Test.stl, square_tower.stl]
2024-01-03 Pictures and Updates
    Added the long awaited example pictures for two steps.
    Updated readme to resolve issue #2. Also updated it to include more information and fix typos.
    Remodeled the minimum layer speed cone to prevent missing layer errors when slicing and so that the cone actually comes out round and not 20-something sided.
    [Minimum-Layer-Speed-Cone.stl]
2024-02-20 Model Hotfix
    [Minimum-Layer-Time-Test.3mf]
